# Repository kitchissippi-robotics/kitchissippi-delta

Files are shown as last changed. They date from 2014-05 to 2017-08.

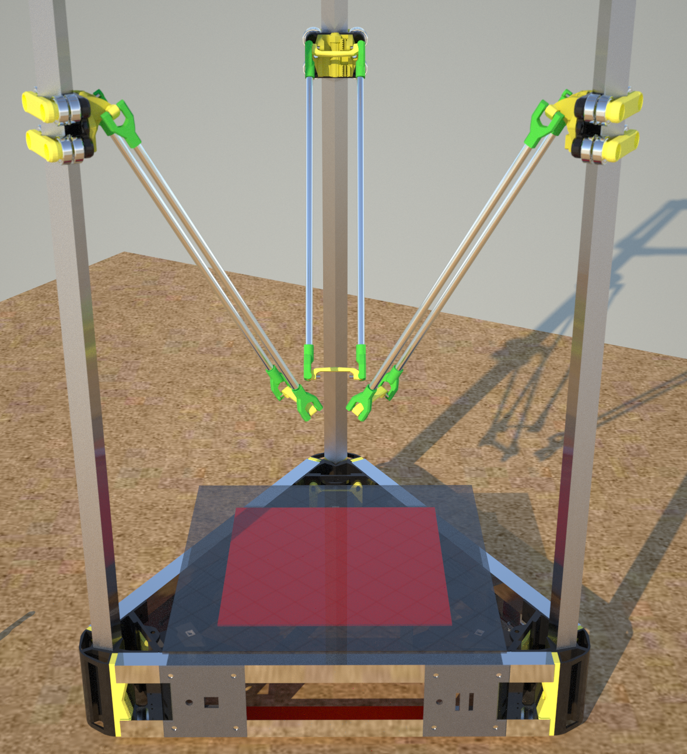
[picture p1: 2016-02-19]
Test Renderings/Kitchissippi Delta v0.3.png

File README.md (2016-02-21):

#Kitchissippi Delta 3D Printer

The Kitchissippi Delta is a prototype delta style 3D printer designed by Brian Cantin.<br>

The early versions have proven that the concept works well, however it requires refinement.<br>
Home Page: [Kitchissippi Robotics](https://kitchissippi-robotics.com/3d-printers/kitchissippi-delta/)

## Version Notes

v3.2 - OpenSCAD Based design start, largely inspired by the Kitchissippi Robotics Gemini 3D printer work in OpenSCAD. Much cleanup of the build is in progress and start of a common code library.

## Design Philosophy

This 3D printer is born out of a philosophy that encompasses many points:

1. As much of the machine should be made out of 3D printed plastic items as is reasonably possible, and these parts should fit within the print area of a Prusa Mendel i2.
   * Frame joining pieces, effector, linear carriages, etc.
   * The parts that make this machine fit together and be an FFM printer are all plastic and smaller than 200mm x 200m x 100mm.
   * Some parts may not fit within the restrictions of PrintrBot or Huxley models, but this has not been verified nor is it a focus. (Sorry)

2. As much of the hardware which cannot be 3D printed should be commonly available at North American hardware store chains.
  * Frame is made from 3/4" steel and aluminum square tubing stocked by most large chain stores
  * Parallelogram rods are made from round aluminum rods stocked by most large chain stores
  * Core design uses SAE hardware as much as possible, the primary exceptions being NEMA17 bolts as the motor format is metric by nature - I'm not going to re-drill and re-thread my motors and neither should you.
  * Build platform uses 1' x 1' mirror tile
  * While the unholy mix of metric and SAE that makes up this printer might be considered strange, it's based on availability of parts on the continent it was designed on - see point 6 if you're elsewhere.

3. If possible, recycled parts from commonly found machinery should be used.
  * The belt drive uses 608zz bearings for the idlers. These can be found in unused skateboards or rollerblades, or easily available from sporting goods stores that sell such items.
  * All joints use bicycle chain pins - these are hardened steel pins and can be extracted with an inexpensive tool from old chains or even sourced from new chains which are quite inexpensive.

4. Use standard RepRap electronics where possible.
  * This machine is designed around the RUMBA controller but could easily be controlled with a RAMPS + ATMega board
  * This machine is designed around a 12v LED power supply, but can be also run on a salvaged ATX PSU from a computer since it uses the 12v standard.

5. This design is scalable.
  * By changing the vertical tubing you can realistically make the build volume as large or small as you desire.
  * By changing the horizontal frame tubing and parallelogram arm lengths proportionally, you can make the build area as large or small as you desire.

6. Make the design parametric where possible.
  * This point doesn't hold as much priority but is kept in consideration.
  * The SAE bolt sizing chosen for much of the prototype builds is quite close to M4 and for the most part one should be able to directly replace the SAE hardare with metric if care is taken during assembly.
  * As the design gets migrated into an SCAD design, the options for this will increase.

##Build and Design Notes

###Pin Swivels

- Each swivel joint has <i>(6) Pins</i> inserted into a <u>Pin Swivel Arm</u>
- Each <u>Rod End</u> will be attached to the rod and glued into place while level
- <u>Rod Ends</u> will then snap-fit over the pins on the <u>Pin Swivel Arm</u>
- This is done for two rods per axis and on both ends of the rods
- This creates a paralellogram of two rod assemblies with a <u>Pin Swivel Arm<u> at each end

####Parts for the assembly:
- (6) 300mm x 6.4mm round aluminum rod
- (36) 7.8mm x 3.6mm round steel bicycle chain pins (note be careful when using chain scraps that all 36 pins are the same size)
- (6) printed <u>Pin Swivel Arm</u>
- (12) printed <u>Rod End</u>

###Drive System:

- GT2 timing belt driven on machined aluminum GT2-20 pulleys with 608zz bearing idlers.
- Linear motion achieved on 3/4" hand sanded and polished steel tubing, with 608zz carriage sytem based on the K-02 prototype carriage concept.
- Consideration was given to spectra-line drive systems, however the relative cost of GT2 belt and the extra effort required seems economically unsound.
- Standard NEMA17 stepper motors.

###Extrusion:

- 1.75mm filament driven through 2mm ID / 4mm OD PTFE tubing.
- Carriage and mounts are based around the current J Head design with no consideration for other groovemounted hotends at this time - it will be made more modular in the future
- Fan shrouding is designed for the needs of a J Head running at elevated temperatures, there is a 25mm x 10mm fan aimed at the cooling fins in the PEEK/cold-end portion of the design - always on.
- Ducting may be beneficial to other similar hotends, however I would not recommend using the Effector - Core piece with an all-metal hotend unless it has been printed in a high temperature plastic, such as ABS or Nylon
- Dual 25mm x 10mm fans ducted around the hotend towards the print immediately below the carriage for plastics that need active cooling - software controlled.
- The above description of the effector unit will be completely revised in v3.2 with the aim of cooling only the hotend fins, the dual 25mm print cooling fans provided negligible benefits

###Movement:

- Universal joints created using pins extracted from used bicycle chain.
- Joints have a snap-assemble design but are not very conducive to repeated disassembly.
- Using 1/4" solid aluminum rod for the carriage arms, will need to be glued into the universal joint arms.
- The control arms parallelogram borrows the swivel bar concept from the DeltaPi design, although this implementation is quite different

###Calibration:

- Initial build will not have consideration for auto-levelling.<br>
  Once the base design has matured from an initial testing prototype to a working proof consideration can be applied to such advanced topics.

###Assembly Notes:

- The universal joint arms may split if you try to force them onto the carriage arms.<br>
  I recommend printing them in PLA and then dipping them in hot water for 10 seconds to soften the plastic before carefully pushing them over the rods for a dry-run fitting.<br>
  Let them cool on the rod before removing them to dry them off so that you retain the internal shape.<br>

- The universal joint has some play to it it's movement, this has mostly been eliminated in current prototypes.<br>
  There is provision for spring attachments between the effector arm pairs on each side, like on the 3DR - this should help keep everything tight<br>
  Apply thick grease to the pin holders on the carriages.<br>

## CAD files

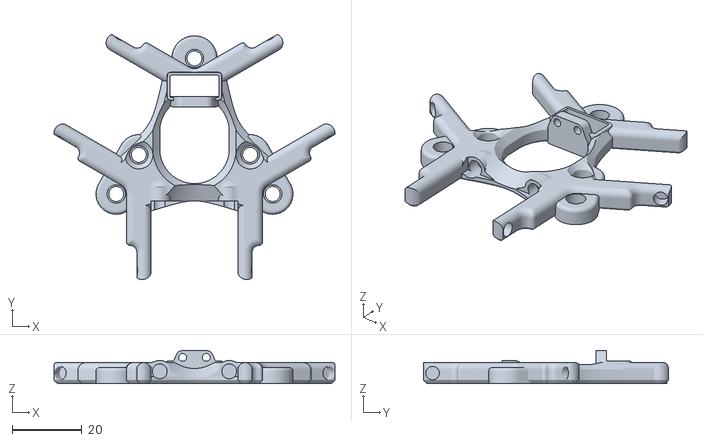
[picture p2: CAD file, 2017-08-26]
F360/Effector Base.stl
80.9 x 70.5 x 9.50

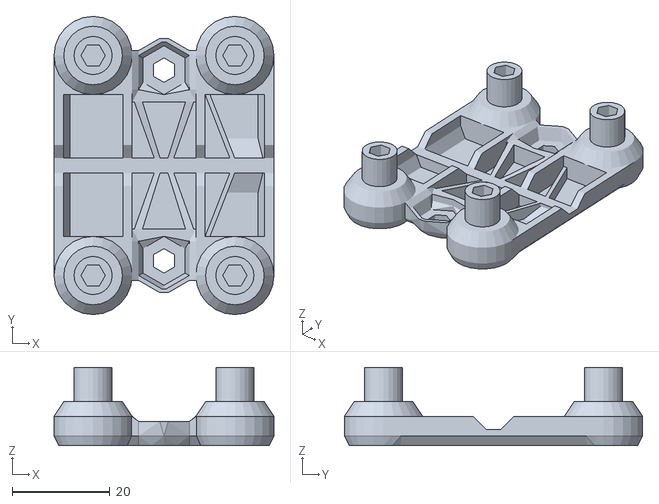
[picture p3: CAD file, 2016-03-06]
OpenSCAD/carriage_inside.stl
45.0 x 61.0 x 16.0

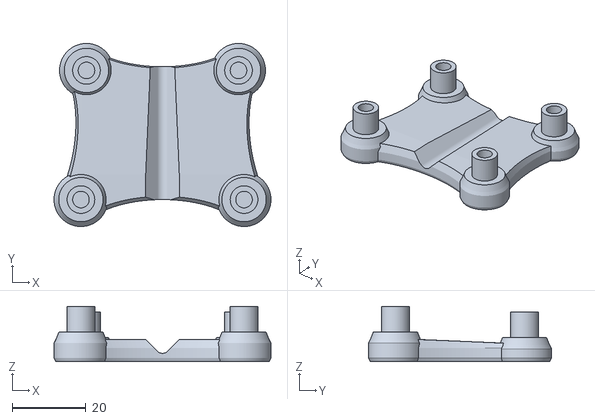
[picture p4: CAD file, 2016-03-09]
OpenSCAD/STL Exports/Carriage_Outer.stl
58.8 x 49.6 x 15.0

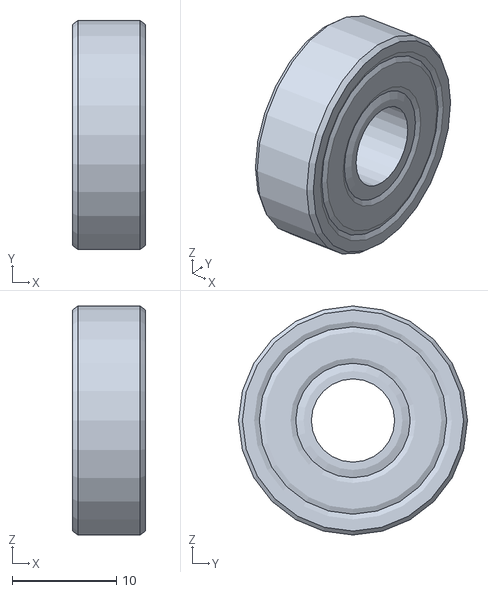
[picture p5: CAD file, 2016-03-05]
OpenSCAD/Vitamins/608_bearing.stl
7.00 x 22.0 x 22.0

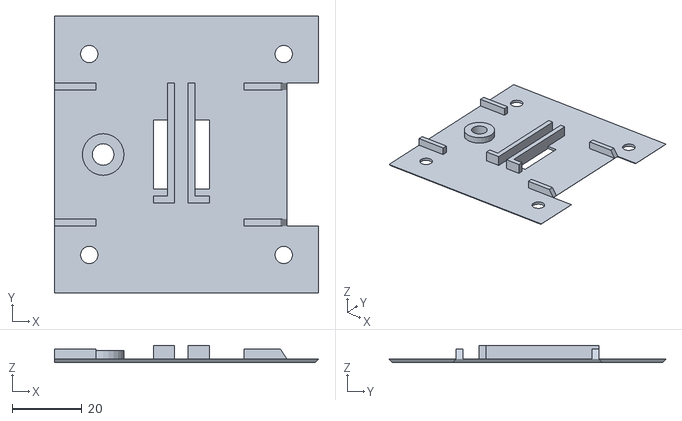
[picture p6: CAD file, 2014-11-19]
STL/Base Face Panels/Power Panel.stl
76.0 x 79.6 x 5.00

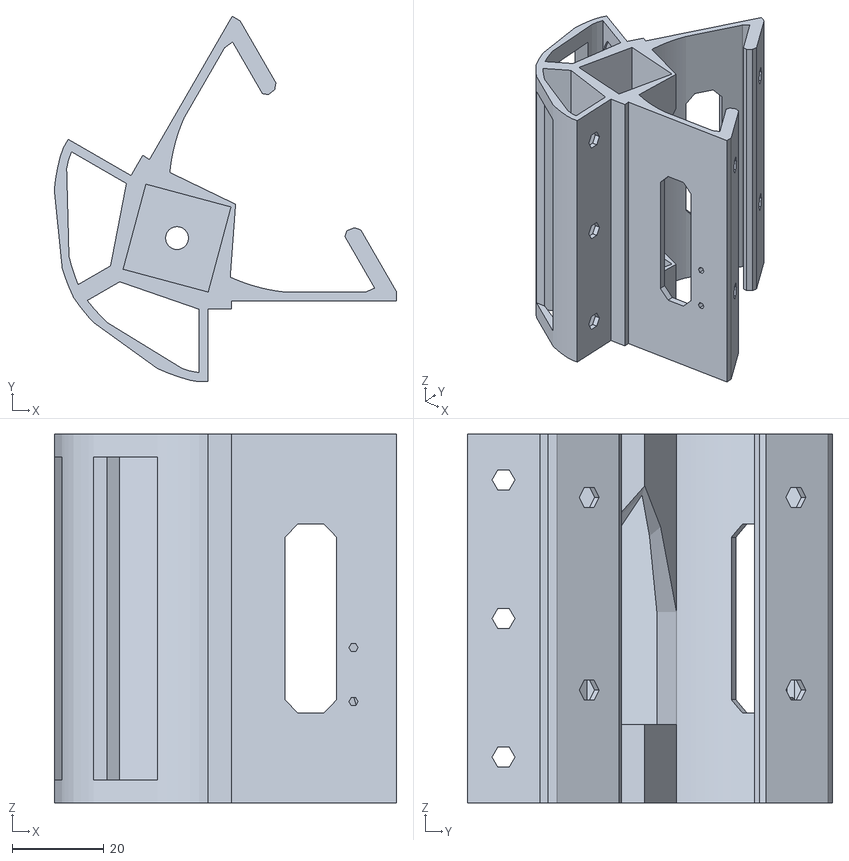
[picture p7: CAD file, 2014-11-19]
STL/Base Frame Pieces/Bottom Corner.stl
74.6 x 79.6 x 80.4

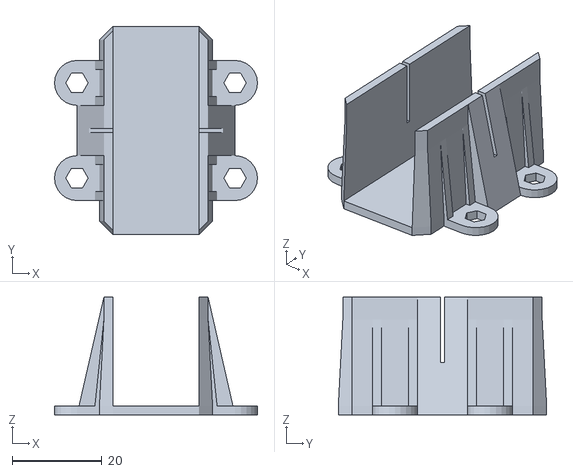
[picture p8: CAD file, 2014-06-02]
STL/Build Tools/Frame Jig Slotted.stl
45.2 x 46.4 x 26.2

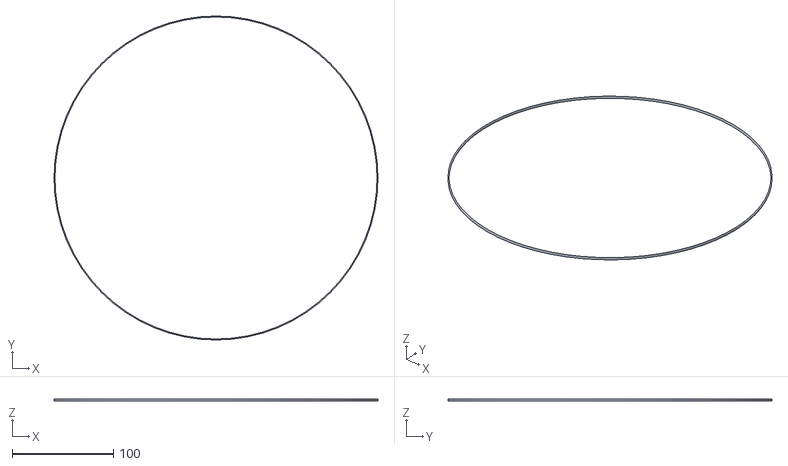
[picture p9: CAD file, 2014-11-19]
STL/Calibration Pieces/160mm Circle.stl
320.0 x 320.0 x 2.00

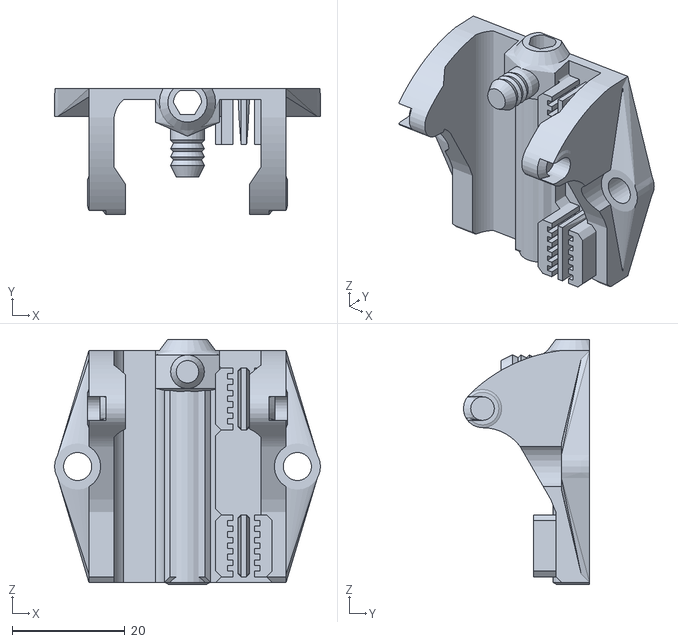
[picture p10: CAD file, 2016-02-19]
STL/Carriage Pieces/Carriage Adapter.stl
47.2 x 22.4 x 43.5

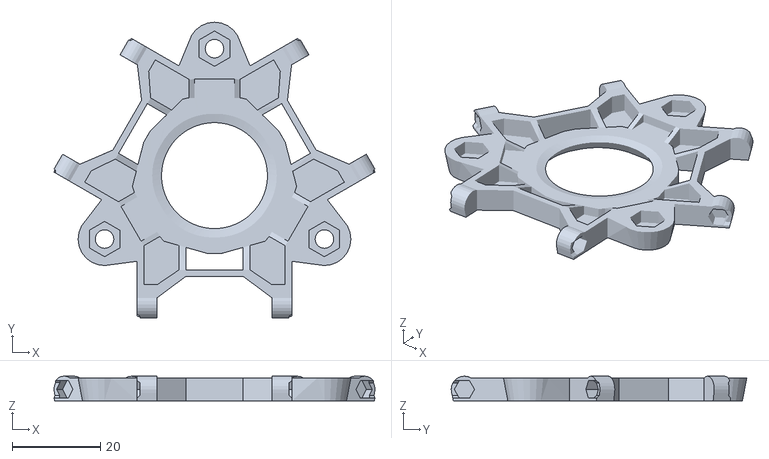
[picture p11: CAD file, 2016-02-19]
STL/Effector Pieces/Effector - Mockup (repaired).stl
72.7 x 66.9 x 5.62

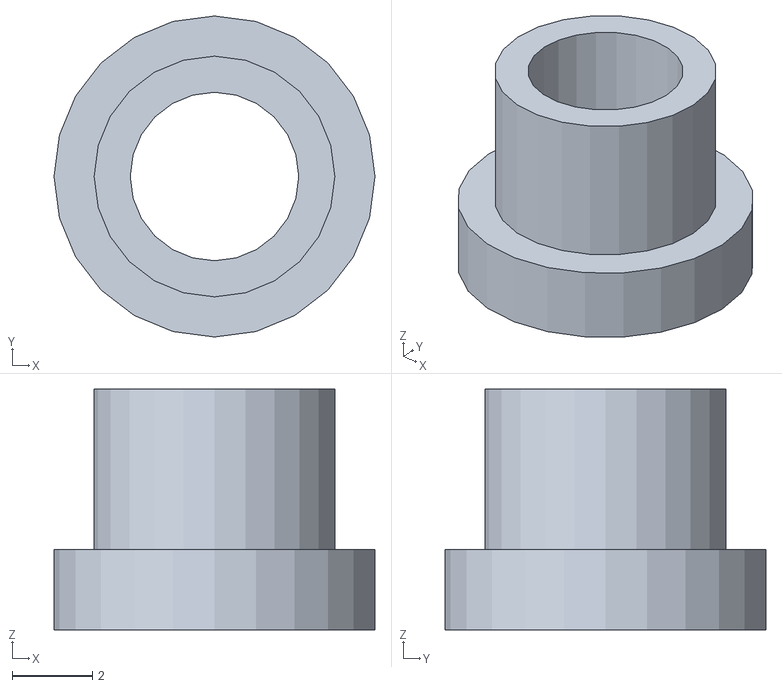
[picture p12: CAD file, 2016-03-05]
STL/PushfitBowden.stl
8.00 x 8.00 x 6.00

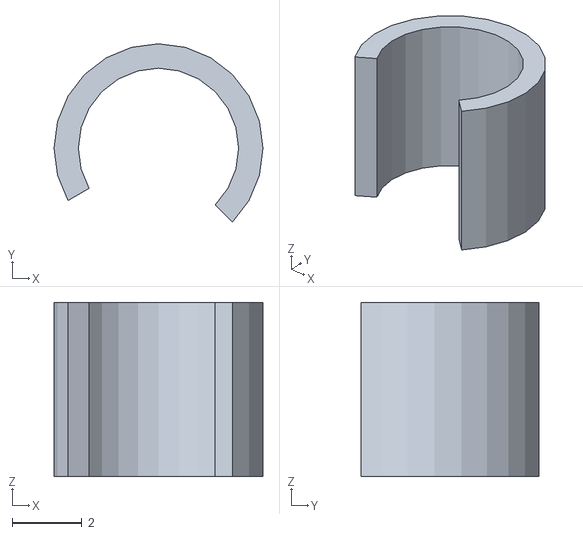
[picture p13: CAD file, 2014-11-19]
STL/Test Pieces/Bearing Collar.stl
6.00 x 5.12 x 5.00

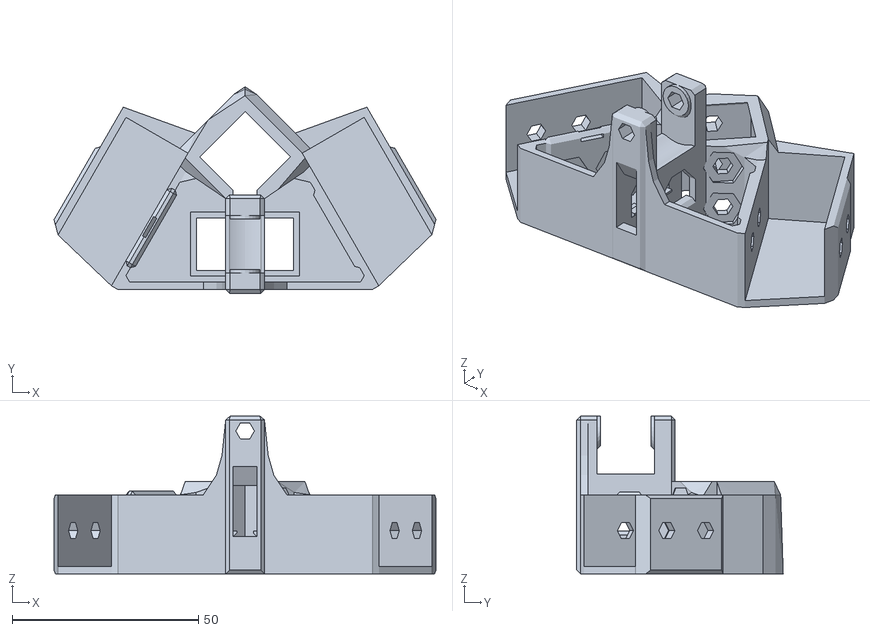
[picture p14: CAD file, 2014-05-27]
STL/Top Frame Pieces/Corner Top Idler.stl
102.4 x 55.4 x 42.3

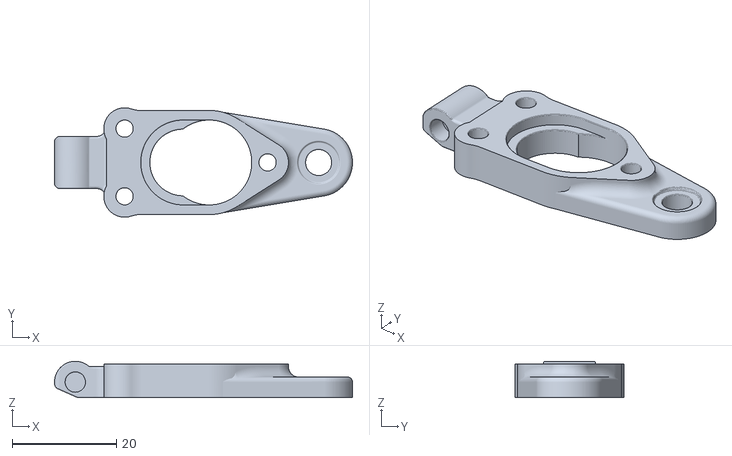
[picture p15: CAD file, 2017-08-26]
F360/Effector Groove Mount.stl
57.2 x 21.0 x 7.00

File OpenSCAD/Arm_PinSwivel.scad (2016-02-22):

// *********************************************************************************************************************
// ( )/ )(_  _)(_  _)___(  _ \(  _  )(  _ \(  _  )(_  _)(_  _)/ __)/ __)
//  )  (  _)(_   )( (___))   / )(_)(  ) _ < )(_)(   )(   _)(_( (__ \__ \
// (_)\_)(____) (__)    (_)\_)(_____)(____/(_____) (__) (____)\___)(___/
// *********************************************************************************************************************
// Kitchissippi Delta 3D Printer - Prototype
//
// Written by bcantin@kitchissippi-robotics.com
// Copyright (c) 2015 Kitchissippi Robotics
// ---------------------------------------------------------------------------------------------------------------------
// Pin_Swivel_Arm.scad
// *********************************************************************************************************************

include <Configuration.scad>
include <Dimensions.scad>
include <OpenSCAD-Hardware/HardwareLib.scad>

// Determine if MultiPartMode is enabled - if not, render the part automatically
// and enable support material (if it is defined)


if (undef == MultiPartMode) {
	MultiPartMode = false;
	EnableSupport = true;

	Part_Pin_Swivel_Arm();
	Hardware_Pin_Swivel_Arm();
} else {
	EnableSupport = false;
}

module Part_Pin_Swivel_Arm() {
	difference() {
		union() {
			// Right Side Pin Holder
			hull() {
				// Right base for the vertical pins
				translate([-rpArm_Spacing /2, 0, 0])
					cylinder(h = rpSwivelArmHeight, d = hwPin_Diameter + 3, $fn = gcFacetMedium);

				// Right base for the horizontal pins
				translate([-rpArm_Spacing /2 + hwPin_Diameter /2 + rpArm_PinSeparation, 0, -(hwPin_Length - rpArm_PinDepth) + hwPin_Length + (rpArm_PinSeparation /2)])
				rotate([0,90,0])
					cylinder(h = rpArm_PinDepth, d = hwPin_Diameter +3, $fn = gcFacetMedium);

				// Right base for the horizontal pins
				*translate([-rpArm_Spacing /2 + hwPin_Diameter /2 + rpArm_PinSeparation, 0, -(hwPin_Length - rpArm_PinDepth) + hwPin_Length + (rpArm_PinSeparation /2)])
				rotate([0,90,0])
					cylinder(h = rpArm_PinDepth - 2, d = rpSwivelArmHeight, $fn = gcFacetMedium);

				// Right base for the vertical pins
				translate([-rpArm_Spacing /2 + 5, - 5, 0])
					cylinder(h = rpSwivelArmHeight, d = 6, $fn = gcFacetSmall);
			}

			// Joining Arm
			difference() {
				offset = 10;
				diameter = 14;

				hull() {
					// Left base for the vertical pins
					translate([-rpArm_Spacing /2 + 5, - 5, 0])
						cylinder(h = rpSwivelArmHeight, d = 6, $fn = gcFacetSmall);

					// Right base for the vertical pins
					translate([rpArm_Spacing /2 - 5, - 5, 0])
						cylinder(h = rpSwivelArmHeight, d = 6, $fn = gcFacetSmall);

					translate([-rpArm_Spacing /2 + offset /2 + 1, -4, -(hwPin_Length - rpArm_PinDepth) + hwPin_Length + (rpArm_PinSeparation /2)])
					rotate([0,90,0])
						cylinder(h = rpArm_Spacing - offset - 2, d = rpSwivelArmHeight, $fn = gcFacetMedium);
				}

				// carve out access space
				translate([-rpArm_Spacing /2 + offset /2, 0, -(hwPin_Length - rpArm_PinDepth) + hwPin_Length + (rpArm_PinSeparation /2)])
				rotate([0,90,0])
				cylinder(h = rpArm_Spacing - offset, d = diameter, $fn = gcFacetMedium);

				// carve out access space
				*translate([-rpArm_Spacing /2 + offset /2, 1, -(hwPin_Length - rpArm_PinDepth) + hwPin_Length + (rpArm_PinSeparation /2)])
				rotate([0,90,0])
				cylinder(h = rpArm_Spacing - offset, d = diameter + 2, $fn = gcFacetMedium);
			}

			// Left Side Pin Holder
			hull() {
				// Left base for the vertical pins
				translate([rpArm_Spacing /2, 0, 0])
					cylinder(h = rpSwivelArmHeight, d = hwPin_Diameter + 3, $fn = gcFacetMedium);

				// Left base for the horizontal pins
				translate([rpArm_Spacing /2 - hwPin_Diameter /2 - rpArm_PinSeparation, 0, -(hwPin_Length - rpArm_PinDepth) + hwPin_Length + (rpArm_PinSeparation /2)])
					rotate([0,-90,0])
						cylinder(h = rpArm_PinDepth, d = hwPin_Diameter +3, $fn = gcFacetMedium);

				// Left base for the horizontal pins
					*translate([rpArm_Spacing /2 - hwPin_Diameter /2 - rpArm_PinSeparation, 0, -(hwPin_Length - rpArm_PinDepth) + hwPin_Length + (rpArm_PinSeparation /2)])
					rotate([0,-90,0])
						cylinder(h = rpArm_PinDepth - 2, d = rpSwivelArmHeight, $fn = gcFacetMedium);

				// Left base for the vertical pins
				translate([rpArm_Spacing /2 - 5, - 5, 0])
					cylinder(h = rpSwivelArmHeight, d = 6, $fn = gcFacetSmall);
			}
		}

		// carve out pins

		// Left vertical pins
		translate([-rpArm_Spacing /2, 0, -(hwPin_Length - rpArm_PinDepth)])
			cylinder(h = hwPin_Length, d = HW_Hole(hwPin_Diameter), $fn=gcFacetSmall);

		translate([-rpArm_Spacing /2, 0, -(hwPin_Length - rpArm_PinDepth) + hwPin_Length + rpArm_PinSeparation])
			cylinder(h = hwPin_Length, d = HW_Hole(hwPin_Diameter), $fn=gcFacetSmall);

		// Right vertical pins
		translate([rpArm_Spacing /2, 0, -(hwPin_Length - rpArm_PinDepth)])
			cylinder(h = hwPin_Length, d = HW_Hole(hwPin_Diameter), $fn=gcFacetSmall);

		translate([rpArm_Spacing /2, 0, -(hwPin_Length - rpArm_PinDepth) + hwPin_Length + rpArm_PinSeparation])
			cylinder(h = hwPin_Length, d = HW_Hole(hwPin_Diameter), $fn=gcFacetSmall);

		// Left horizontal pin
		translate([-rpArm_Spacing /2 + hwPin_Diameter /2 + rpArm_PinSeparation, 0, -(hwPin_Length - rpArm_PinDepth) + hwPin_Length + (rpArm_PinSeparation /2)])
		rotate([0,90,0])
			cylinder(h = hwPin_Length, d = HW_Hole(hwPin_Diameter), $fn=gcFacetSmall);

		// Right horizontal pin
		translate([rpArm_Spacing /2 - hwPin_Diameter /2 - rpArm_PinSeparation, 0, -(hwPin_Length - rpArm_PinDepth) + hwPin_Length + (rpArm_PinSeparation /2)])
		rotate([0,-90,0])
			cylinder(h = hwPin_Length, d = HW_Hole(hwPin_Diameter), $fn=gcFacetSmall);


	}
}

// *********************************************************************************************************************
// Draw Hardware (for reference)
// ---------------------------------------------------------------------------------------------------------------------

module Hardware_Pin_Swivel_Arm() {
// Left vertical pins
translate([-rpArm_Spacing /2, 0, -(hwPin_Length - rpArm_PinDepth)])
	Draw_Pin();

translate([-rpArm_Spacing /2, 0, -(hwPin_Length - rpArm_PinDepth) + hwPin_Length + rpArm_PinSeparation])
	Draw_Pin();

// Right vertical pins
translate([rpArm_Spacing /2, 0, -(hwPin_Length - rpArm_PinDepth)])
	Draw_Pin();

translate([rpArm_Spacing /2, 0, -(hwPin_Length - rpArm_PinDepth) + hwPin_Length + rpArm_PinSeparation])
	Draw_Pin();

// Left horizontal pin
translate([-rpArm_Spacing /2 + hwPin_Diameter /2 + rpArm_PinSeparation, 0, -(hwPin_Length - rpArm_PinDepth) + hwPin_Length + (rpArm_PinSeparation /2)])
rotate([0,90,0])
	Draw_Pin();

// Right horizontal pin
translate([rpArm_Spacing /2 - hwPin_Diameter /2 - rpArm_PinSeparation, 0, -(hwPin_Length - rpArm_PinDepth) + hwPin_Length + (rpArm_PinSeparation /2)])
rotate([0,-90,0])
	Draw_Pin();
}

// *********************************************************************************************************************
// Hardware Reference (TODO: Migrate to a global include file for use in other parts)
// ---------------------------------------------------------------------------------------------------------------------

module Draw_Pin() {
	%cylinder(h = hwPin_Length, d = hwPin_Diameter, $fn=gcFacetSmall);
}

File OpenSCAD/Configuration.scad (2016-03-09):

// *********************************************************************************************************************
// ( )/ )(_  _)(_  _)___(  _ \(  _  )(  _ \(  _  )(_  _)(_  _)/ __)/ __)
//  )  (  _)(_   )( (___))   / )(_)(  ) _ < )(_)(   )(   _)(_( (__ \__ \
// (_)\_)(____) (__)    (_)\_)(_____)(____/(_____) (__) (____)\___)(___/
// *********************************************************************************************************************
// Kitchissippi Delta 3D Printer - Prototype
//
// Written by bcantin@kitchissippi-robotics.com
// Copyright (c) 2014-2016 Kitchissippi Robotics
// ---------------------------------------------------------------------------------------------------------------------
// Configuration.scad
// Does not generate any parts, used for project global configuration
// *********************************************************************************************************************

// Set this to true if using Metric hardware instead of SAE
// NOTE - this functionality is incomplete, SAE is design default
// Ultimately the Kitchissippi-Delta is a mix of hardware types

HARDWARE_METRIC = false;

//

NOZZLE_SIZE = 0.5;
RENDER_LEVEL =4 ;	// use 1 for screen quality, 4 for print quality
SLICER_COMPENSATION = 0.0;

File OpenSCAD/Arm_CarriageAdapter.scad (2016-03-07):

// *********************************************************************************************************************
// ( )/ )(_  _)(_  _)___(  _ \(  _  )(  _ \(  _  )(_  _)(_  _)/ __)/ __)
//  )  (  _)(_   )( (___))   / )(_)(  ) _ < )(_)(   )(   _)(_( (__ \__ \
// (_)\_)(____) (__)    (_)\_)(_____)(____/(_____) (__) (____)\___)(___/
// *********************************************************************************************************************
// Kitchissippi Delta 3D Printer - Prototype
//
// Written by bcantin@kitchissippi-robotics.com
// Copyright (c) 2015 Kitchissippi Robotics
// ---------------------------------------------------------------------------------------------------------------------
// CarriageAdapter.scad
// *********************************************************************************************************************

include <Configuration.scad>
include <Dimensions.scad>
include <OpenSCAD-Hardware/HardwareLib.scad>

// Determine if MultiPartMode is enabled - if not, render the part automatically
// and enable support material (if it is defined)

if (undef == MultiPartMode) {
	MultiPartMode = false;
	EnableSupport = true;

	Part_CarriageAdapter();
	Hardware_CarriageAdapter();
} else {
	EnableSupport = false;
}

// ---------------------------------------------------------------------------------------------------------------------

module Part_CarriageAdapter() {
	difference() {
		// main shape
		union() {
			CarriageAdapter_Base();

			hull() {
				// washer base
				translate([0, -rpCarriageAdapter_AdjustmentWasherOffset + 2.5, rpCarriageAdapter_AdjustmentBoltOffset])
				rotate([90,90,0])
					cylinder(h = 2.5, d = 12, $fn = gcFacetMedium);

				// adjuster nut base
				translate([0, -rpCarriageAdapter_AdjustmentNutOffset + 0.5, rpCarriageAdapter_AdjustmentBoltOffset])
				rotate([90,90,0])
					cylinder(h = 5, d = 15, $fn = 6);

				// adjuster bolt cover
				translate([0, -12, rpCarriageAdapter_AdjustmentBoltOffset])
				rotate([90,90,0])
					cylinder(h = 2, d = 8, $fn = gcFacetMedium);
			}

			hull() {
				// adjuster bolt cover
				translate([0, 2.5, rpCarriageAdapter_AdjustmentBoltOffset])
				rotate([90,90,0])
					cylinder(h = 15, d = 8, $fn = gcFacetMedium);

				// adjuster bolt cover
				/*translate([0, 14, 2])
				rotate([90,90,0])
					cylinder(h = 30, d = 8, $fn = gcFacetMedium);

				// adjuster bolt cover
				translate([0, 16, 2])
				rotate([90,90,0])
					cylinder(h = 30, d = 6, $fn = gcFacetMedium);

				// adjuster bolt cover
				translate([0, 20, 0])
				rotate([90,90,0])
					cylinder(h = 30, d = 2, $fn = gcFacetMedium);*/

				translate([0, 10, 2])
					sphere(d = 6, $fn = gcFacetSmall);
			}

			translate([-rpCarriageAdapter_BeltPathOffset,8,0])
			CarriageBase_BeltClamp(12);

			translate([-rpCarriageAdapter_BeltPathOffset,-20,0])
			CarriageBase_BeltClamp(12);
			//CarriageAdapter_SwivelArm();
		}

		// carve outs
		translate([-rpCarriageAdapter_BeltPathOffset,8,0])
			CarriageBase_BeltCarveOut(12);

				translate([-rpCarriageAdapter_BeltPathOffset,-20,0])
			CarriageBase_BeltCarveOut(12);

		// swivel surface carveout
		translate([rpArm_Spacing /2 -8,0, rpCarriageAdapter_SwivelOffset])
		rotate([0,90,0])
			cylinder(h = 5, d = 12, $fn=gcFacetSmall);

		mirror([1,0,0])
		translate([rpArm_Spacing /2 -8,0, rpCarriageAdapter_SwivelOffset])
		rotate([0,90,0])
			cylinder(h = 5, d = 12, $fn=gcFacetSmall);

		// Right horizontal pin
		translate([-rpArm_Spacing /2 + hwPin_Diameter /2 + rpArm_PinSeparation, 0, rpCarriageAdapter_SwivelOffset])
		rotate([0,90,0])
			cylinder(h = hwPin_Length + 0.5, d = HW_Hole(hwPin_Diameter), $fn=gcFacetSmall);

		// Right horizontal pin mounting slot
		hull() {
		translate([-rpArm_Spacing /2 + hwPin_Diameter /2 + rpArm_PinSeparation , 0, rpCarriageAdapter_SwivelOffset +6])
		rotate([0,105,0])
			cylinder(h = hwPin_Length, d = HW_Hole(hwPin_Diameter), $fn=gcFacetSmall);
		translate([-rpArm_Spacing /2 + hwPin_Diameter /2 + rpArm_PinSeparation -1, 0, rpCarriageAdapter_SwivelOffset + 2])
		rotate([0,105,0])
			cylinder(h = hwPin_Length, d = HW_Hole(hwPin_Diameter), $fn=gcFacetSmall);
		}

		// Left horizontal pin
		translate([rpArm_Spacing /2 - hwPin_Diameter /2 - rpArm_PinSeparation, 0, rpCarriageAdapter_SwivelOffset])
		rotate([0,-90,0])
			cylinder(h = hwPin_Length + 1, d = HW_Hole(hwPin_Diameter), $fn=gcFacetSmall);

		// left horizontal pin mounting slot
		mirror([1,0,0]) hull() {
		translate([-rpArm_Spacing /2 + hwPin_Diameter /2 + rpArm_PinSeparation , 0, rpCarriageAdapter_SwivelOffset +6])
		rotate([0,105,0])
			cylinder(h = hwPin_Length, d = HW_Hole(hwPin_Diameter), $fn=gcFacetSmall);
		translate([-rpArm_Spacing /2 + hwPin_Diameter /2 + rpArm_PinSeparation -1, 0, rpCarriageAdapter_SwivelOffset + 2])
		rotate([0,105,0])
			cylinder(h = hwPin_Length, d = HW_Hole(hwPin_Diameter), $fn=gcFacetSmall);
		}

		// adjuster bolt
		translate([0, 0, rpCarriageAdapter_AdjustmentBoltOffset])
		rotate([90,0,0])
			Carve_hwBolt(hwNo8_Bolt_PanHead, 30);

		// mounting bolts

		translate([-rpCarriageAdapter_MountSpacing /2,0, -12 + rpCarriageAdapter_BaseBoltThickness])
				Carve_hwBolt(hwNo8_Bolt_PanHead, 12);

		translate([rpCarriageAdapter_MountSpacing /2,0, -12 + rpCarriageAdapter_BaseBoltThickness])
				Carve_hwBolt(hwNo8_Bolt_PanHead, 12);

		hull() {
			translate([-rpCarriageAdapter_MountSpacing /2,0, 5])
				cylinder(h = 2.5, d = 9, $fn = gcFacetMedium);

			translate([-rpCarriageAdapter_MountSpacing /2,0, 5])
				cylinder(h = 5, d = 8, $fn = gcFacetMedium);

			translate([-rpCarriageAdapter_MountSpacing /2,0, 10])
				sphere(d = 8, $fn = gcFacetMedium);
		}

		hull() {
			translate([rpCarriageAdapter_MountSpacing /2,0, 5])
				cylinder(h = 2.5, d = 9, $fn = gcFacetMedium);

			translate([rpCarriageAdapter_MountSpacing /2,0, 5])
				cylinder(h = 5, d = 8, $fn = gcFacetMedium);

			translate([rpCarriageAdapter_MountSpacing /2,0, 10])
				sphere(d = 8, $fn = gcFacetMedium);
		}

		// adjuster nut
		translate([0, -rpCarriageAdapter_AdjustmentNutOffset - 0, rpCarriageAdapter_AdjustmentBoltOffset])
		rotate([90,90,0])
			cylinder(h = 4, d = 11, $fn = 6);



		// base block carveout
		translate([-50, -50, -20])
			cube([100, 100, 20]);
	}
}

// ---------------------------------------------------------------------------------------------------------------------

module CarriageBase_BeltCarveOut(length) {
	height = 10.1 - rpCarriageAdapter_BaseThickness;
		translate([1, -0.1, rpCarriageAdapter_BaseThickness])
			cube([1, length + 0.2, height]);

		translate([-2, -0.1, rpCarriageAdapter_BaseThickness])
			cube([1, length + 0.2, height]);

		for (i = [0 : 2 : length]) {
			translate([2, i, rpCarriageAdapter_BaseThickness])
			scale([2.5,1,1])
			cylinder(h = height, d = 1, $fn = gcFacetSmall);

			translate([-2, i, rpCarriageAdapter_BaseThickness])
			scale([2.5,1,1])
			cylinder(h = height, d = 1, $fn = gcFacetSmall);
		}
}

// ---------------------------------------------------------------------------------------------------------------------

module CarriageBase_BeltClamp(length) {
		hull() {
			// --
			translate([rpCarriageAdapter_BeltPathWidth/2, length -1, 0])
			scale([2,1,1])
				cylinder( h = 2, d = 2, $fn = gcFacetSmall);

			translate([rpCarriageAdapter_BeltPathWidth/2, length -1, 8])
				sphere(d = 2, $fn = gcFacetSmall);

			// --
			translate([-rpCarriageAdapter_BeltPathWidth/2, length -1, 0])
			scale([2,1,1])
				cylinder( h = 2, d = 2, $fn = gcFacetSmall);

			translate([-rpCarriageAdapter_BeltPathWidth/2, length -1, 8])
				sphere(d = 2, $fn = gcFacetSmall);

			// --
			translate([rpCarriageAdapter_BeltPathWidth/2, 1, 0])
			scale([2,1,1])
				cylinder( h = 2, d = 2, $fn = gcFacetSmall);

			translate([rpCarriageAdapter_BeltPathWidth/2, 1, 8])
				sphere(d = 2, $fn = gcFacetSmall);

			// --
			translate([-rpCarriageAdapter_BeltPathWidth/2, 1, 0])
			scale([2,1,1])
				cylinder( h = 2, d = 2, $fn = gcFacetSmall);

			translate([-rpCarriageAdapter_BeltPathWidth/2, 1, 8])
				sphere(d = 2, $fn = gcFacetSmall);
		}

}

// ---------------------------------------------------------------------------------------------------------------------

module CarriageAdapter_Base() {
	difference() {
		union() {
			hull() {
				// bolt bases
				translate([-rpCarriageAdapter_MountSpacing /2,0, 0])
					cylinder(h = rpCarriageAdapter_BaseBoltThickness, d = 8, $fn = gcFacetMedium);

				translate([rpCarriageAdapter_MountSpacing /2,0, 0])
					cylinder(h = rpCarriageAdapter_BaseBoltThickness, d = 8, $fn = gcFacetMedium);

				// four corners
				translate([rpCarriageAdapter_BaseWidth /2, rpCarriageAdapter_BaseLength /2, 0])
					cylinder(h = rpCarriageAdapter_BaseThickness, d = 4, $fn = gcFacetSmall);

				translate([rpCarriageAdapter_BaseWidth /2, -rpCarriageAdapter_BaseLength /2, 0])
					cylinder(h = rpCarriageAdapter_BaseThickness, d = 4, $fn = gcFacetSmall);
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

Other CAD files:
OpenSCAD/STL Exports/Carriage_Inner.stl
STL/Base Face Panels/Vent Panel.stl
STL/Base Frame Pieces/Lower Frame Mount.stl
STL/Build Tools/Frame Jig End.stl
SCAD/Configuration.scad
F360/Single Bowden Cap.stl
F360/Swivel Bracket Left.stl
F360/Swivel Bracket Right.stl
OpenSCAD/Arm_RodEnd.scad
OpenSCAD/Assemblies/Carriage_Render.scad
OpenSCAD/Carriage_Common.scad
OpenSCAD/Carriage_Inner.scad
OpenSCAD/Carriage_Outer.scad
OpenSCAD/Dimensions.scad
OpenSCAD/Effector_Base.scad
OpenSCAD/Effector_Knurled_Thumbscrews.scad
OpenSCAD/Effector_LockRing.scad
OpenSCAD/STL Exports/Arm_CarriageAdapter.stl
OpenSCAD/STL Exports/Arm_PinSwivel.stl
OpenSCAD/STL Exports/Arm_RodEnd.stl
OpenSCAD/STL Exports/Effector_Base.stl
OpenSCAD/STL Exports/Effector_LockRing.stl
OpenSCAD/Vitamins/hotend-hexagon.scad
OpenSCAD/Vitamins/hotend-jhead.scad
SCAD/Arm_CarriageAdapter.scad
SCAD/CarriageAdapter.scad
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

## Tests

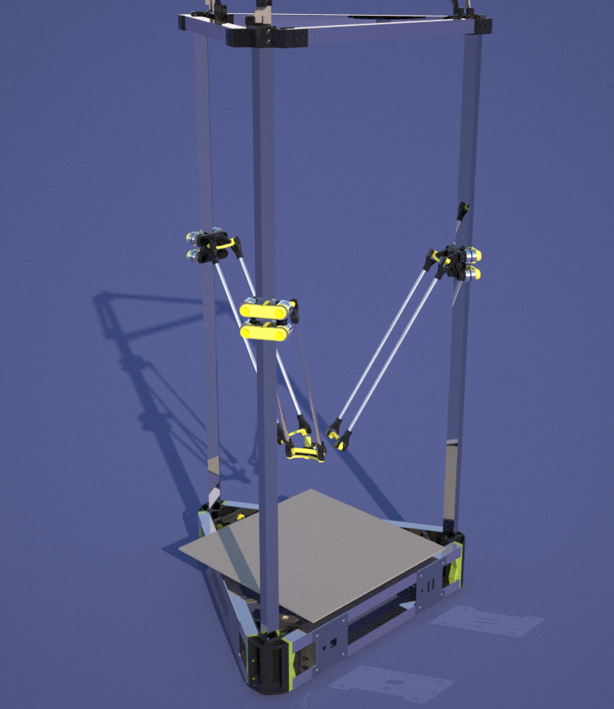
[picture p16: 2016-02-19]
Test Renderings/Mockup.png

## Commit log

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2014-04-06 Start of u joint
    [U Joint Dev.skp, U Joint Dev~.skp]
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2014-04-06 First Test Print Piece
    [U Joint Dev.stl]
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2014-04-06 Tighter Tolerances
    [Holder Dev.stl, U Joint Dev.stl]
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2014-04-07 Added template of carriage design
    [U Joint Dev.skp, U Joint Dev~.skp]
2014-04-07 Carriage STL (not printed)
    [Carriage Dev.stl, U Joint Dev.skp, U Joint Dev~.skp]
2014-04-08 j head snap-fit groove mount :)
    Love me some snap-fit
    [Carriage Dev.stl, Groovemount Test.stl, U Joint Dev.skp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]
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2014-04-08 First attempt at adding 25mm shroud... needs work
    [U Joint Dev.skp, U Joint Dev~.skp]
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2014-04-09 I hate designing ducts
    [U Joint Dev.skp, U Joint Dev~.skp]
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2014-04-09 Hating Ducts... This one is OK ish
    [U Joint Dev.skp, U Joint Dev~.skp]
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2014-04-09 Did I mention I dislike making ducts?
    [U Joint Dev.skp, U Joint Dev~.skp]
2014-04-09 shaun is a troll
    [Shroud Dev.stl, U Joint Dev.skp, U Joint Dev~.skp]
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2014-04-12 Screw Guides etc, added
    [U Joint Dev.skp, U Joint Dev~.skp]
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2014-04-12 Added material for screw holes
    [U Joint Dev.skp, U Joint Dev~.skp]
2014-04-12 Basic 1/3rd shroud designed
    [U Joint Dev.skp, U Joint Dev~.skp]
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2014-04-12 Most of central duct created
    [U Joint Dev.skp, U Joint Dev~.skp]
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2014-04-14 Fixed STL Export
    [Bowden Attachement.stl]
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2014-04-14 Slight update to carriage before print
    [Carriage.stl]
2014-04-15 Creating Mock up of whole printer
    [Delta.skp]
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2014-04-19 Shorter Tower
    [Delta.skp]
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2014-04-20 1 segment of carriage
    [Delta.skp]
2014-04-20 Export Failing
    [Carriage v2.stl, Delta.skp]
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2014-04-21 Working at frame dimensioning
    [Delta.skp]
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2014-04-21 Shoe-horned thread onto carriage
    [Delta.skp]
2014-04-21 Tower Redesign
    [Delta.skp]
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2014-04-22 Carriage v6 Export 1
    [Carriage v6-1.obj]
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2014-04-22 Screw Hole Fail
2014-04-22 Revert fe5b8f2..88393d5
    This rolls back to commit fe5b8f2fe0e0c8fe32e10a9dee48d664458e9428.
    [Carriage v6-1.obj, Carriage v6-1.stl, Carriage v6.obj]
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2014-04-22 Carriage v6-3 pre print
    [Carriage v6-2.obj, Carriage v6-3.obj, Carriage v6-3.stl]
2014-04-22 Post print fix
    [Carriage v6-4.obj, Carriage v6-4.stl]
2014-04-22 Joint Fix, Project Re-Org, Cleanup
    Tighter fit on the universal joint core pins
    Created OBJ, SCAD folder
    Added OpenSCAD file for threading scripts
    Re-organized files
    Removed outdated dev models
    Pre-Merging to core project
    [Carriage Dev.stl, Carriage v2.stl, Carriage v4.obj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]
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2014-04-23 Simple Threaded Duct (ABS)
    [J Head Duct.stl]
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2014-04-28 K03 v0.0.7 - Sketchup Roll Back
    Export / Import performed via dae to Sketch Up Make 2013 edition which
    has a working STL export.
    OBJ file capability is a Pro only feature.
    [Delta v7.stl, Effector v7 Test.stl, Swivel Bar.stl]
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2014-04-28 New Swivel Mount / Fan Mount Test Part
    [Swivel Mount.stl]
2014-04-28 Revert "New Swivel Mount / Fan Mount Test Part"
    This reverts commit e1805a60ce2247c95c4068b0478a4ec59c34fb24.
    Conflicts:
    SKP/Delta v7.skp
    SKP/Delta v7~.skp
    [Swivel Mount.stl]
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2014-04-29 New Cowling Piece for testing
    [3x Swivel Bar.stl]
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2014-04-29 Updated partial part for test print
    [Partial Effector iii.stl]
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2014-05-04 Changed Swivel Bar Pin-Hole Dimensions
    [Swivel Bar.stl]
2014-05-04 Flex Slots
    [Effector.stl]
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2014-05-05 Printable Carriage Adapter - Oops
    [Carriage Adapter.stl]
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2014-05-09 Fixed swivel bar oversight
    [Arm Holder.stl, Swivel Bar.stl]
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2014-05-12 Test of 1/4 carriage for dimensions with hardware
    [Carriage Quarter Panel.stl]
2014-05-12 Major Cleanup of files and removal of dead-end dev
    [3x Swivel Bar.stl, Bowden Swivel.stl, Carriage - J Head Bowden Mount.stl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]
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2014-05-12 Test outside part - incorrect
    [Carriage Outside.stl]
2014-05-12 Carriage Outer Bearing Holder
    [Carriage Outside.stl]
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2014-05-13 Rough Draft Carriage Adapter
    [Carriage Adapter.stl]
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2014-05-14 Fixed Carriage Adapter
    [Carriage Adapter.stl]
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2014-05-20 Revert e765136..ef9060a
    This rolls back to commit e76513671adb5a8100762980b1c33f02a3ef6197.
    [Carriage Outside Fancy.stl, Carriage Outside.stl]
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2014-05-20 New outside carriage piece
    [Carriage Outside.stl]
2014-05-20 Slight thickness added back to side walls,
    [Carriage Outside.stl]
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2014-05-21 Reinforced Mini Carriage
    [Carriage Inside New.stl]
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2014-05-22 Adapter Work - Needs Belt clamps
    [Carriage Adapter New.stl]
2014-05-22 New Carriage Adapter
    ISO Grid Support, new clamps, etc.
    [Carriage Adapter New.stl]
2014-05-22 Tighter belt clamp, longer arm pilons
    [Carriage Adapter New.stl]
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2014-05-26 Slight Revisions to Idler Corner
    [Corner Top Idler.stl]
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2014-05-26 Added lip at top
    [Corner Top Idler.stl]
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2014-05-27 Updated Idler, started bottom corner
    [Corner Top Idler.stl]
2014-05-27 Added nut traps for Idler Corner
    [Corner Top Idler.stl]
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2014-05-27 Updated Wire Guide on Top Corner
    [Corner Top Idler.stl]
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2014-05-29 Once Side Mostly Created
    [Corner Bottom.stl]
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2014-06-02 Frame Cutting Jig Pieces
    [Frame Jig End.stl, Frame Jig Slotted.stl, Frame Jig.skp]
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2014-06-19 Test pieces - good dimensions
    [Bearing Collar.stl, Bearing Spacer.stl, Carriage Bearing Post.stl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]
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2014-11-05 Test Expansion Plug Mount
    [Lower Frame Mount.stl, Plug Test.skp, Plug Test~.skp]
2014-11-05 Concept for Keyhole mount
    [Plug Test.skp, Plug Test~.skp]
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2014-11-06 Fixed orientation
    [Plug Test.stl]
2014-11-06 Awesome part is awesome
    [Lower Frame Mount.stl, Plug Test.skp, Plug Test~.skp]
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2014-11-06 Start of new bottom alignment
    [Plug Test.skp]
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2014-11-07 Adding curves and keyholes
    [Frame Parts Plate.amf, Lower Frame Mount.stl, Plug Test.skp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]
2014-11-07 Added new test corner
    [Bottom Corner.stl]
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2014-11-07 Fixed path for test bottom corner
    [Bottom Corner.stl]
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2014-11-08 Close, but will revert and modify
    [Stabilizer Plate.stl]
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2014-11-08 Stabilizer Plate - Needs Fixed Holes
    [Stabilizer Plate.stl]
2014-11-08 Fixed Holes
    [Stabilizer Plate.stl]
2014-11-10 AC Plug Plate Test
    [AC Plug Plate.stl]
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2014-11-10 Added blank side panels
    [Mockup.stl]
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2014-11-12 reinforced power panels
    [AC Plug Panel.stl, AC Switch Panel.stl]
2014-11-12 Corrected orientation
    [Blank Panel.stl, Power Panel.stl]
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2015-01-27 Minor change to thumbscrews
    [Effector Knurled Thumbscrews.scad]
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2016-02-19 Start of library work
    [LinearCarriage_Common.scad, LinearCarriage_Outer.scad, LinearCarriage_Render.scad]
2016-02-20 Start of new library usage and parts
    [Configuration.scad, LinearCarriage_Render.scad, Pin Swivel Arm.scad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]
2016-02-21 Pin Swivel Arm Design
    [Configuration.scad, Pin Swivel Arm.scad, Pin Swivel Arm.stl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]
2016-02-21 Working swivel arm design
    [Pin Swivel Arm.scad]
2016-02-21 Notes update and carriage adapter
    [dimensions.scad]
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2016-02-21 belt path carving is incorrect
    [CarriageAdapter.scad, dimensions.scad]
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2016-02-22 Pin mount slots and belt clamps
    [CarriageAdapter.scad]
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2016-02-22 Modified belt mounts for tighter fit
    [CarriageAdapter.scad, CarriageAdapter.stl]
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2016-02-26 Fixed hotend space
    [Dimensions.scad, Effector_Base.scad, Effector_Base.stl]
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2016-02-27 More corrections for fan mount
    [Dimensions.scad, Effector_Base.scad, Effector_Base.stl]
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2016-02-29 Fixed push fit connector socket
    [Effector_LockRing.scad]
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
